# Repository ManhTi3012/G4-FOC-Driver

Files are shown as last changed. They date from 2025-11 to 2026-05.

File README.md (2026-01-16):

# ⚠️ **WARNING: PROJECT UNDER DEVELOPMENT, CHANGES WILL BE MADE**
<p align="center" style="display: flex; gap: 10px;">
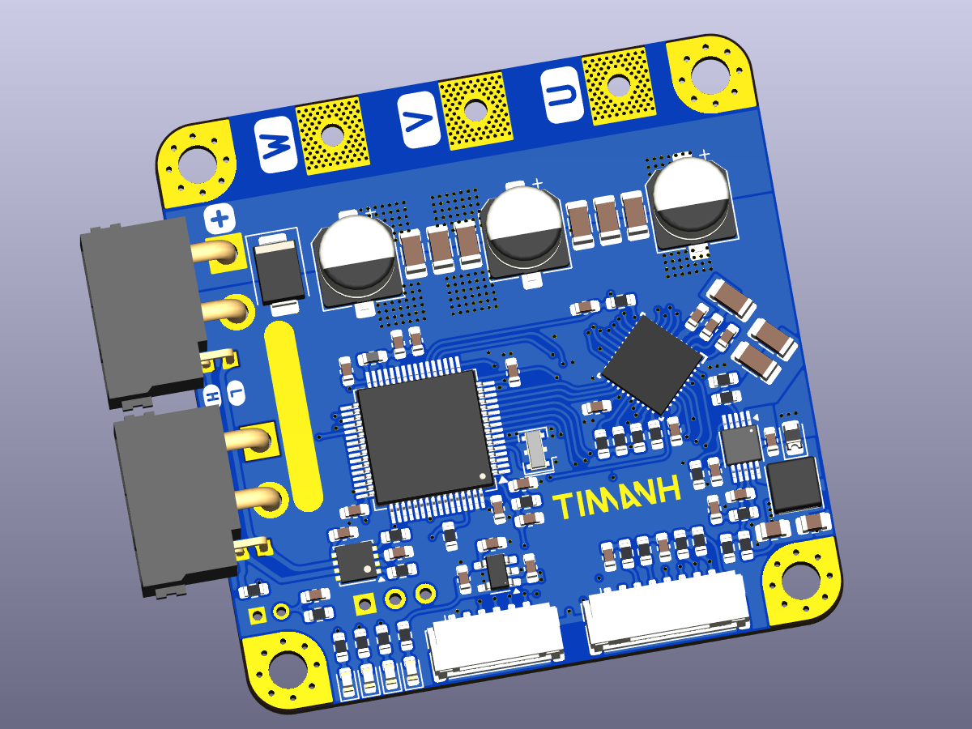
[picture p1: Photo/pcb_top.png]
  
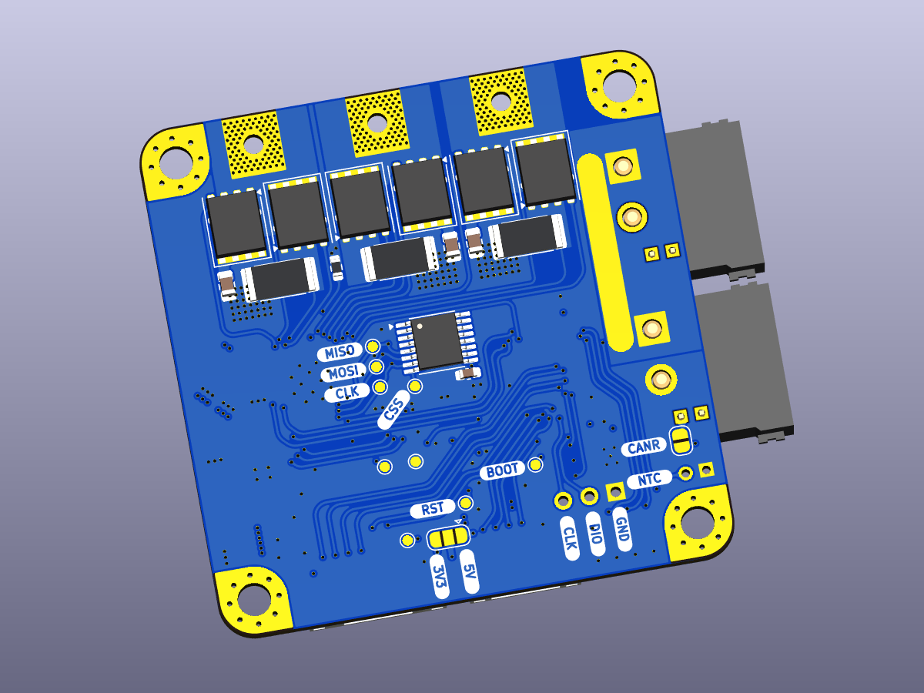
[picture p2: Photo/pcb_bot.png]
  
</p>

# G4-FOC-Driver

# Liability
* The software and hardware are still in development and may contain bugs, errors, or incomplete features.
* Users are encouraged to use this software and hardware responsibly and at their own risk.

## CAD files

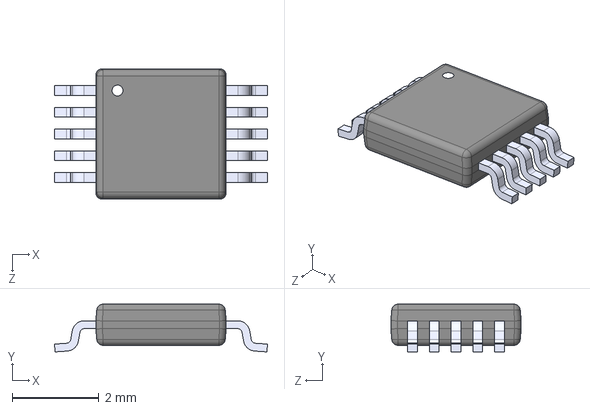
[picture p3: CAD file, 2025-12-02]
Dependencies/HVSSOP-10.STEP
4.90 x 1.10 x 3.00 mm

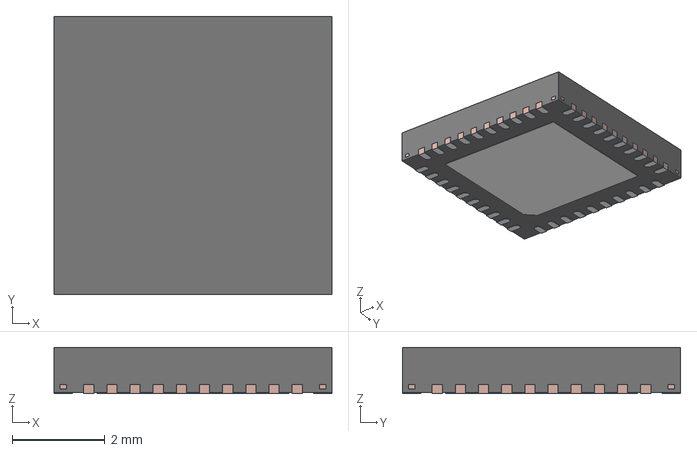
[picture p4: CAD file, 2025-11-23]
Dependencies/ul_DRV8323SRTAT/RTA0040B.stp
6.00 x 6.00 x 1.00 mm
FRAME

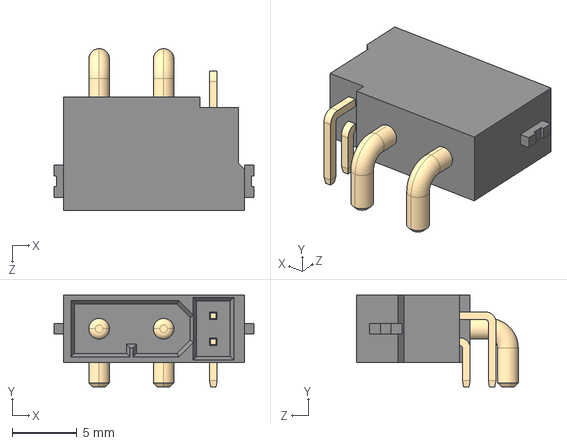
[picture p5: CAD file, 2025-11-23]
Dependencies/XT30PW_2_2_-M.G.B/XT30PW_2_2_-M.G.B.step
15.5 x 7.10 x 12.5 mm

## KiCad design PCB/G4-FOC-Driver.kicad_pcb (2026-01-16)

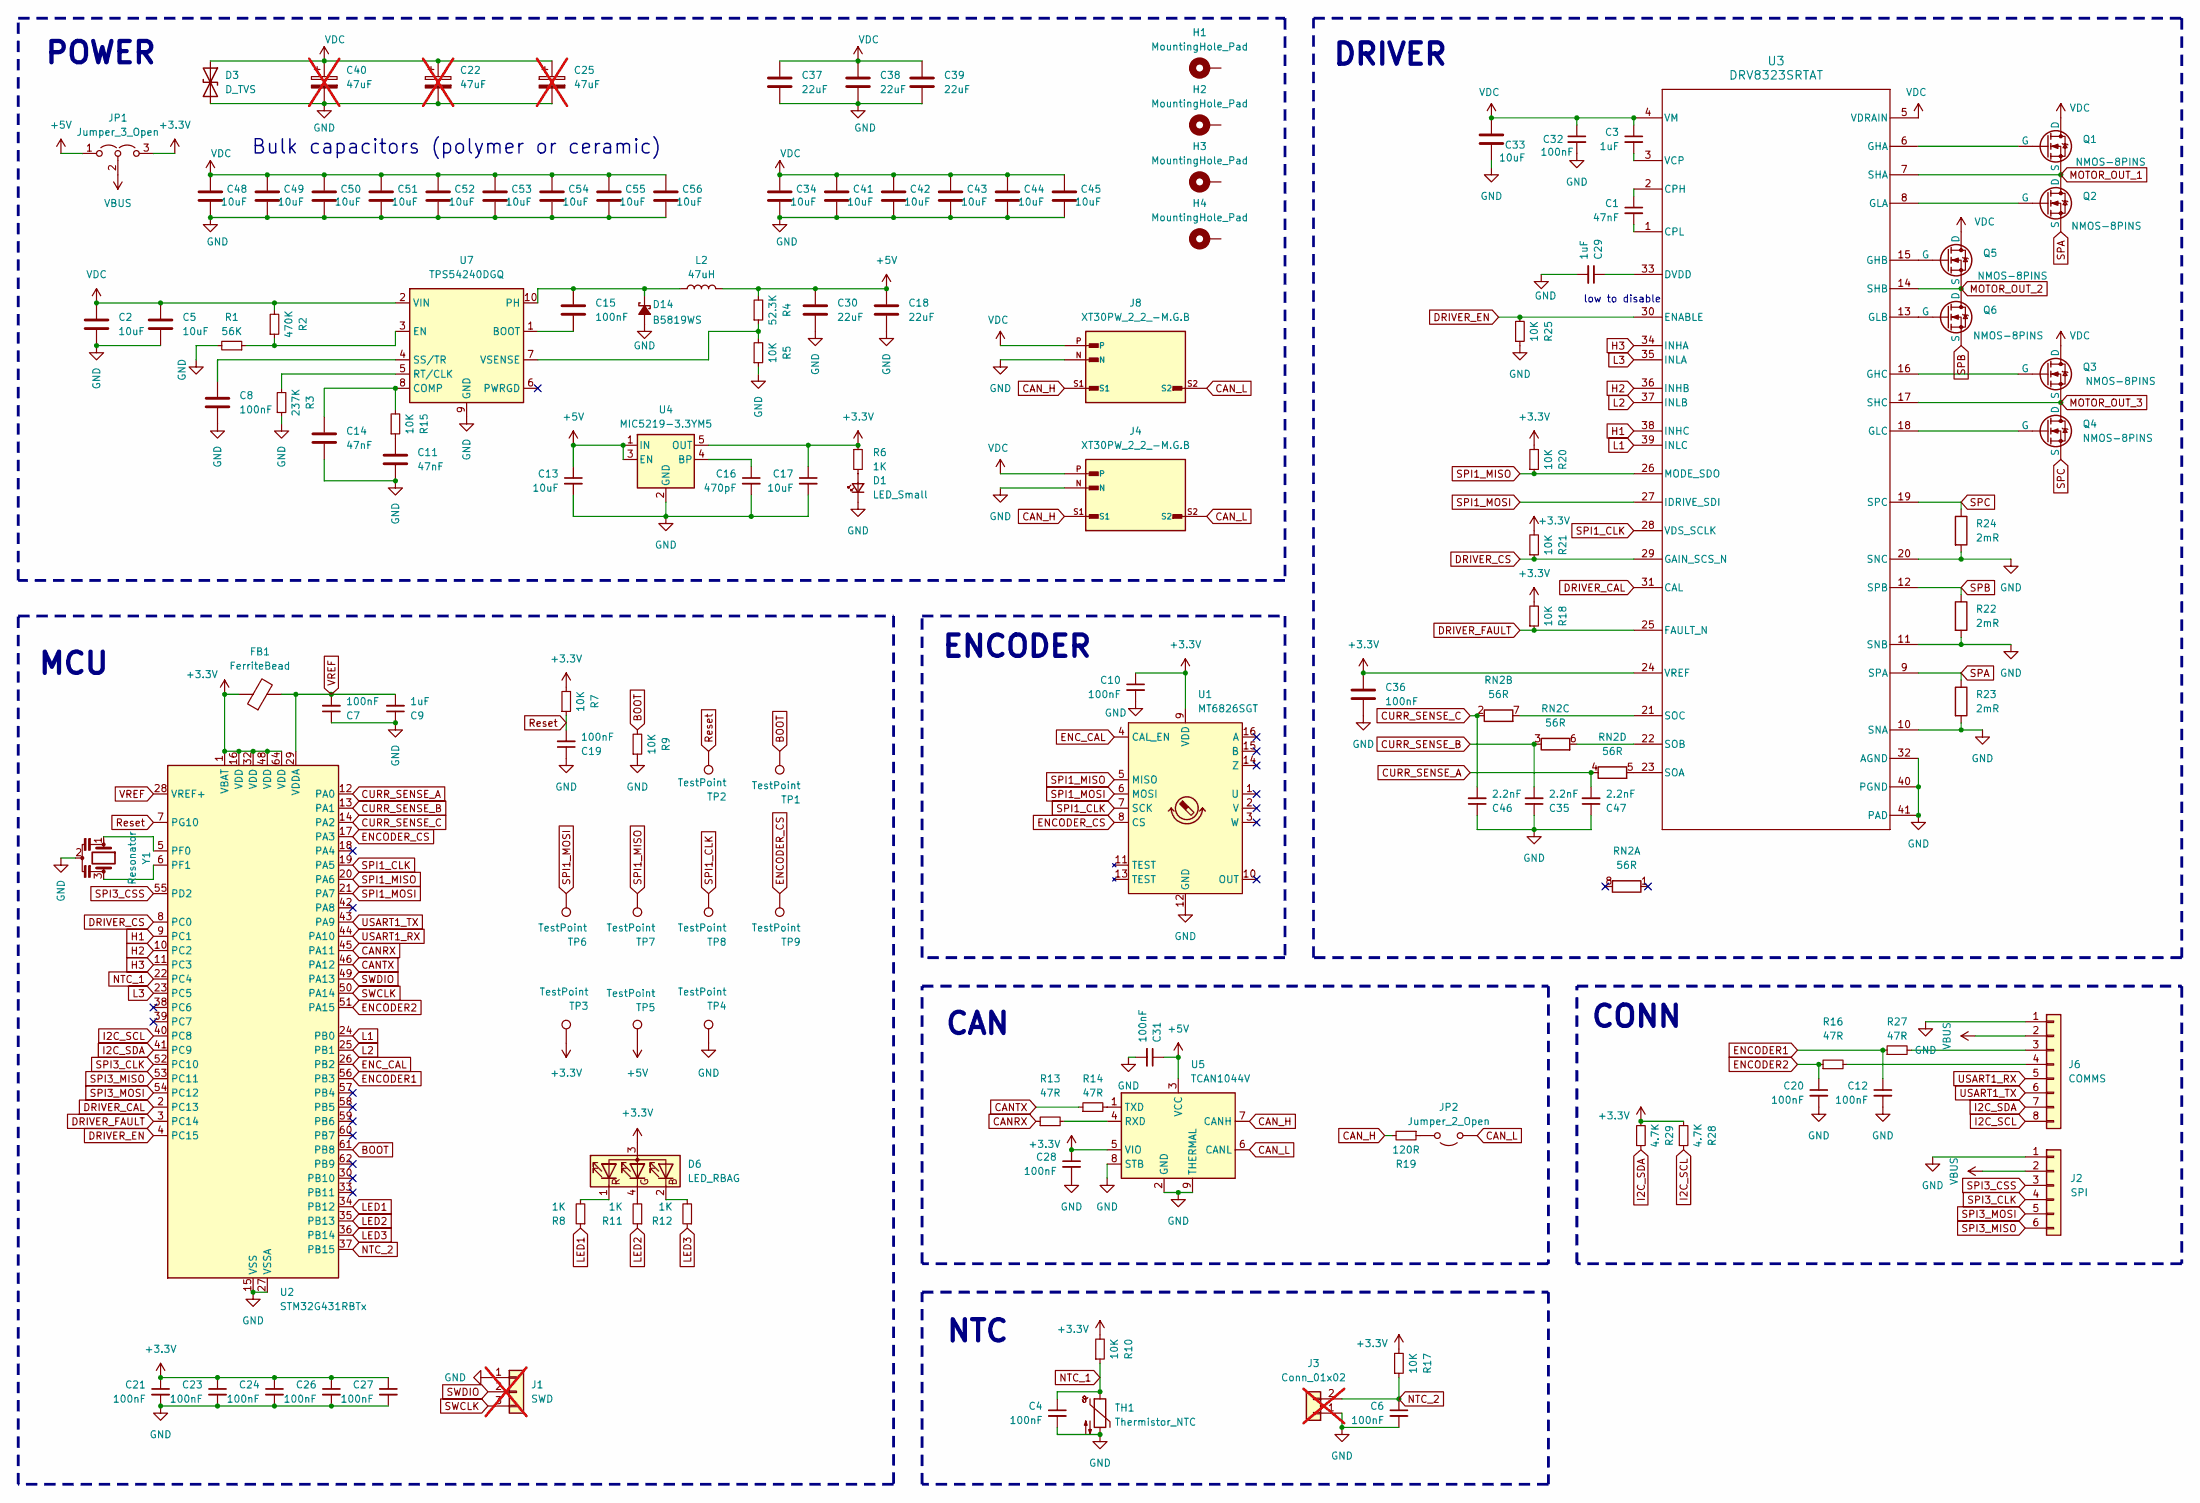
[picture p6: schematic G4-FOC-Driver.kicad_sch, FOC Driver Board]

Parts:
C1, C11, C14: 47nF; C_0603_1608Metric
C2, C5, C33, C34, C41, C42, C43, C44, C45, C48, C49, C50, C51, C52, C53, C54, C55, C56: 10uF; C_1206_3216Metric
C3, C9, C29: 1uF; C_0603_1608Metric
C4, C6, C7, C8, C10, C12, C15, C19, C20, C21, C23, C24, C26, C27, C28, C31, C32, C36: 100nF; C_0603_1608Metric
C13, C17: 10uF; C_0603_1608Metric
C16: 470pF; C_0603_1608Metric
C18, C30, C37, C38, C39: 22uF; C_0805_2012Metric
C22, C25, C40: 47uF; CP_Elec_6.3x5.9; not fitted
C35, C46, C47: 2.2nF; C_0603_1608Metric
D1: LED_Small; LED_0603_1608Metric
D3: D_TVS; D_SMB
D6: LED_RBAG; LED_Cree-PLCC4_2x2mm_CW
D14: B5819WS; D_0805_2012Metric
FB1: FerriteBead; L_0603_1608Metric
H1, H2, H3, H4: MountingHole_Pad; MountingHole_3.2mm_M3_Pad_Via
J1: SWD; PinHeader_1x03_P2.54mm_Vertical; not fitted
J2: SPI; JST_GH_SM06B-GHS-TB_1x06-1MP_P1.25mm_Horizontal
J3: Conn_01x02; PinHeader_1x02_P2.00mm_Vertical; not fitted
J4, J8: XT30PW_2_2_-M.G.B; AMASS_XT30PW_2_2_-M.G.B; PARTREV NA
J6: COMMS; JST_GH_SM08B-GHS-TB_1x08-1MP_P1.25mm_Horizontal
JP1: Jumper_3_Open; SolderJumper-3_P1.3mm_Open_RoundedPad1.0x1.5mm
JP2: Jumper_2_Open; SolderJumper-2_P1.3mm_Open_RoundedPad1.0x1.5mm
L2: 47uH; L_APV_ANR4020
Q1, Q2, Q3, Q4, Q5, Q6: NMOS-8PINS; PQFN-8-EP_6x5mm_P1.27mm_Generic
R1: 56K; R_0603_1608Metric
R2: 470K; R_0603_1608Metric
R3: 237K; R_0603_1608Metric
R4: 52.3K; R_0603_1608Metric
R5, R7, R9, R10, R15, R17, R18, R20, R21, R25: 10K; R_0603_1608Metric
R6, R8, R11, R12: 1K; R_0603_1608Metric
R13, R14, R16, R27: 47R; R_0603_1608Metric
R19: 120R; R_0603_1608Metric
R22, R23, R24: 2mR; R_2512_6332Metric
R28, R29: 4.7K; R_0603_1608Metric
RN2: 56R; R_Array_Convex_4x0402
TH1: Thermistor_NTC; R_0603_1608Metric
TP1, TP2, TP3, TP4, TP5, TP6, TP7, TP8, TP9: TestPoint; TestPoint_Pad_D1.0mm
U1: MT6826SGT; TSSOP-16_4.4x5mm_P0.65mm
U2: STM32G431RBTx; LQFP-64_10x10mm_P0.5mm
U3: DRV8323SRTAT; RTA0040B
U4: MIC5219-3.3YM5; SOT-23-5
U5: TCAN1044V; Texas_S-PVSON-N8_ThermalVias
U7: TPS54240DGQ; HVSSOP-10-1EP_3x3mm_P0.5mm_EP1.57x1.88mm_ThermalVias
Y1: Resonator; Resonator_SMD_Murata_CSTxExxV-3Pin_3.0x1.1mm

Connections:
+3.3V: C10.1, C17.1, C21.1, C23.1, C24.1, C26.1, C27.1, C28.1, C36.1, D6.3 (A), FB1.1, JP1.3 (B), R6.1, R7.2, R10.2, R17.2, R18.2, R20.2, R21.2, R28.2, R29.2, TP3.1, U1.9 (VDD), U2.1 (VBAT), U2.16 (VDD), U2.32 (VDD), U2.48 (VDD), U2.64 (VDD), U3.24 (VREF), U4.5 (OUT), U5.5 (VIO)
+5V: C13.1, C18.2, C30.2, C31.1, JP1.1 (A), L2.2, R4.2, TP5.1, U4.1 (IN), U4.3 (EN), U5.3 (VCC)
BOOT: R9.2, TP1.1, U2.61 (PB8)
CANRX: R13.1, U2.45 (PA11)
CANTX: R14.1, U2.46 (PA12)
CAN_H: J4.S1, J8.S1, R19.2, U5.7 (CANH)
CAN_L: J4.S2, J8.S2, JP2.1 (A), U5.6 (CANL)
CURR_SENSE_A: C47.2, RN2.4 (R4.1), U2.12 (PA0)
CURR_SENSE_B: C35.2, RN2.3 (R3.1), U2.13 (PA1)
CURR_SENSE_C: C46.2, RN2.2 (R2.1), U2.14 (PA2)
DRIVER_CAL: U2.2 (PC13), U3.31 (CAL)
DRIVER_CS: R21.1, U2.8 (PC0), U3.29 (GAIN_SCS_N)
DRIVER_EN: R25.2, U2.4 (PC15), U3.30 (ENABLE)
DRIVER_FAULT: R18.1, U2.3 (PC14), U3.25 (FAULT_N)
ENCODER1: C12.1, R27.1, U2.56 (PB3)
ENCODER2: C20.1, R16.1, U2.51 (PA15)
ENCODER_CS: TP9.1, U1.8 (CS), U2.17 (PA3)
ENC_CAL: U1.4 (CAL_EN), U2.26 (PB2)
GND: C2.1, C4.2, C5.1, C6.2, C7.1, C8.1, C9.1, C10.2, C11.1, C12.2, C13.2, C14.1, C16.2, C17.2, C18.1, C19.1, C20.2, C21.2, C22.2, C23.2, C24.2, C25.2, C26.2, C27.2, C28.2, C29.2, C30.1, C31.2, C32.2, C33.1, C34.1, C35.1, C36.2, C37.1, C38.1, C39.1, C40.2, C41.1, C42.1, C43.1, C44.1, C45.1, C46.1, C47.1, C48.1, C49.1, C50.1, C51.1, C52.1, C53.1, C54.1, C55.1, C56.1, D1.1 (K), D3.2 (A2), D14.2 (A), J1.1, J2.1, J3.1, J4.N, J6.1, J8.N, R1.2, R3.1, R5.1, R9.1, R22.2, R23.2, R24.2, R25.1, TH1.2, TP4.1, U1.12 (GND), U2.15 (VSS), U2.27 (VSSA), U2.31 (VSS), U2.47 (VSS), U2.63 (VSS), U3.10 (SNA), U3.11 (SNB), U3.20 (SNC), U3.32 (AGND), U3.40 (PGND), U3.41 (PAD), U4.2 (GND), U5.2 (GND), U5.8 (STB), U5.9 (THERMAL), U7.9 (GND), U7.11 (GND), Y1.2
H1: U2.9 (PC1), U3.38 (INHC)
H2: U2.10 (PC2), U3.36 (INHB)
H3: U2.11 (PC3), U3.34 (INHA)
I2C_SCL: J6.8, R28.1, U2.40 (PC8)
I2C_SDA: J6.7, R29.1, U2.41 (PC9)
L1: U2.24 (PB0), U3.39 (INLC)
L2: U2.25 (PB1), U3.37 (INLB)
L3: U2.23 (PC5), U3.35 (INLA)
LED1: R8.1, U2.34 (PB12)
LED2: R11.1, U2.35 (PB13)
LED3: R12.1, U2.36 (PB14)
MOTOR_OUT_1: Q1.1 (S), Q1.2 (S), Q1.3 (S), Q2.5 (D), U3.7 (SHA)
MOTOR_OUT_2: Q5.1 (S), Q5.2 (S), Q5.3 (S), Q6.5 (D), U3.14 (SHB)
MOTOR_OUT_3: Q3.1 (S), Q3.2 (S), Q3.3 (S), Q4.5 (D), U3.17 (SHC)
NTC_1: C4.1, R10.1, TH1.1, U2.22 (PC4)
NTC_2: C6.1, J3.2, R17.1, U2.37 (PB15)
unnamed: C11.2, R15.1
unnamed: D1.2 (A), R6.2
unnamed: D6.2 (BK), R12.2
unnamed: D6.4 (GK), R11.2
unnamed: D6.1 (RK), R8.2
unnamed: C15.2, D14.1 (K), L2.1, U7.10 (PH)
unnamed: J6.3, R27.2
unnamed: J6.4, R16.2
unnamed: JP2.2 (B), R19.1
unnamed: Q1.4 (G), U3.6 (GHA)
unnamed: Q2.4 (G), U3.8 (GLA)
unnamed: Q3.4 (G), U3.16 (GHC)
unnamed: Q4.4 (G), U3.18 (GLC)
unnamed: Q5.4 (G), U3.15 (GHB)
unnamed: Q6.4 (G), U3.13 (GLB)
unnamed: RN2.7 (R2.2), U3.21 (SOC)
unnamed: RN2.6 (R3.2), U3.22 (SOB)
unnamed: RN2.5 (R4.2), U3.23 (SOA)
unnamed: U2.5 (PF0), Y1.1
unnamed: U2.6 (PF1), Y1.3
unnamed: C1.1, U3.2 (CPH)
unnamed: C1.2, U3.1 (CPL)
unnamed: C29.1, U3.33 (DVDD)
unnamed: C3.2, U3.3 (VCP)
unnamed: C16.1, U4.4 (BP)
unnamed: R13.2, U5.4 (RXD)
unnamed: R14.2, U5.1 (TXD)
unnamed: C15.1, U7.1 (BOOT)
unnamed: C14.2, R15.2, U7.8 (COMP)
unnamed: R1.1, R2.1, U7.3 (EN)
unnamed: R3.2, U7.5 (RT/CLK)
unnamed: C8.2, U7.4 (SS/TR)
unnamed: R4.1, R5.2, U7.7 (VSENSE)
Reset: C19.2, R7.1, TP2.1, U2.7 (PG10)
SPA: Q2.1 (S), Q2.2 (S), Q2.3 (S), R23.1, U3.9 (SPA)
SPB: Q6.1 (S), Q6.2 (S), Q6.3 (S), R22.1, U3.12 (SPB)
SPC: Q4.1 (S), Q4.2 (S), Q4.3 (S), R24.1, U3.19 (SPC)
SPI1_CLK: TP8.1, U1.7 (SCK), U2.19 (PA5), U3.28 (VDS_SCLK)
SPI1_MISO: R20.1, TP7.1, U1.5 (MISO), U2.20 (PA6), U3.26 (MODE_SDO)
SPI1_MOSI: TP6.1, U1.6 (MOSI), U2.21 (PA7), U3.27 (IDRIVE_SDI)
SPI3_CLK: J2.4, U2.52 (PC10)
SPI3_CSS: J2.3, U2.55 (PD2)
SPI3_MISO: J2.6, U2.53 (PC11)
SPI3_MOSI: J2.5, U2.54 (PC12)
SWCLK: J1.3, U2.50 (PA14)
SWDIO: J1.2, U2.49 (PA13)
USART1_RX: J6.5, U2.44 (PA10)
USART1_TX: J6.6, U2.43 (PA9)
VBUS: J2.2, J6.2, JP1.2 (C)
VDC: C2.2, C3.1, C5.2, C22.1, C25.1, C32.1, C33.2, C34.2, C37.2, C38.2, C39.2, C40.1, C41.2, C42.2, C43.2, C44.2, C45.2, C48.2, C49.2, C50.2, C51.2, C52.2, C53.2, C54.2, C55.2, C56.2, D3.1 (A1), J4.P, J8.P, Q1.5 (D), Q3.5 (D), Q5.5 (D), R2.2, U3.4 (VM), U3.5 (VDRAIN), U7.2 (VIN)
VREF: C7.2, C9.2, FB1.2, U2.28 (VREF+), U2.29 (VDDA)

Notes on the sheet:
ENCODER
Bulk capacitors (polymer or ceramic)
MCU
NTC
POWER
low to disable
DRIVER
CAN
CONN

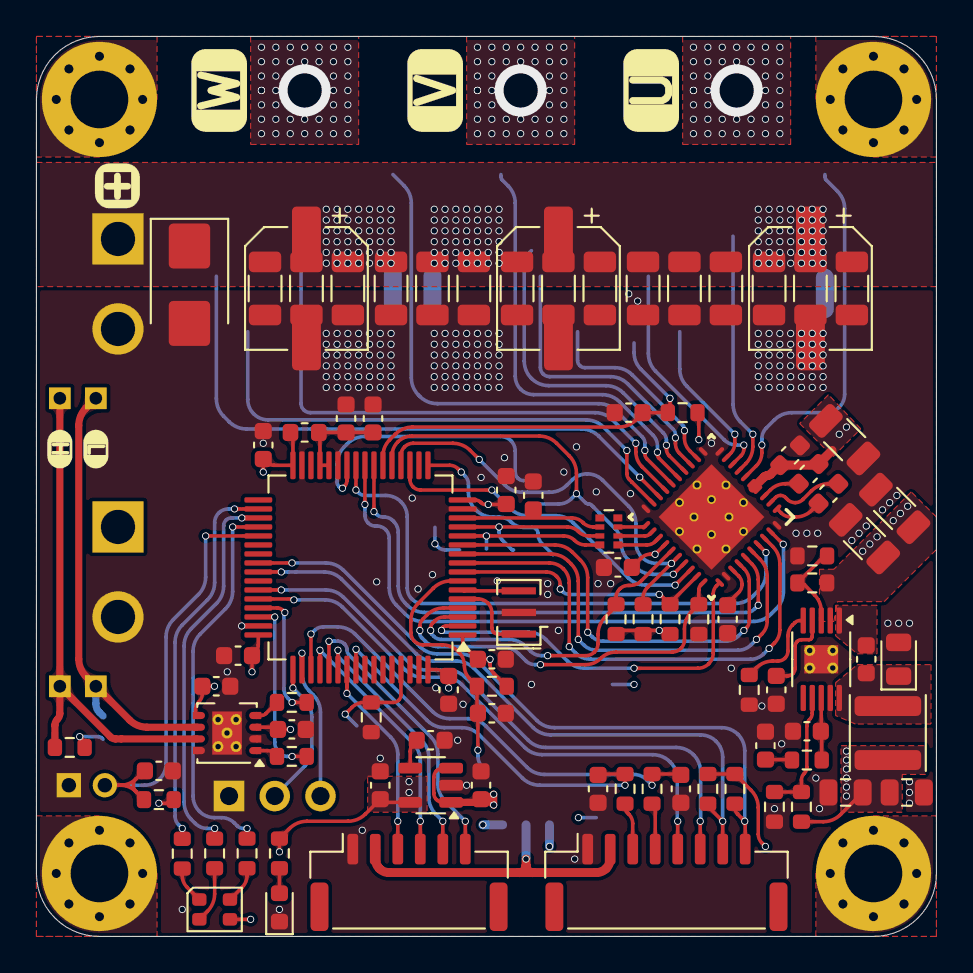
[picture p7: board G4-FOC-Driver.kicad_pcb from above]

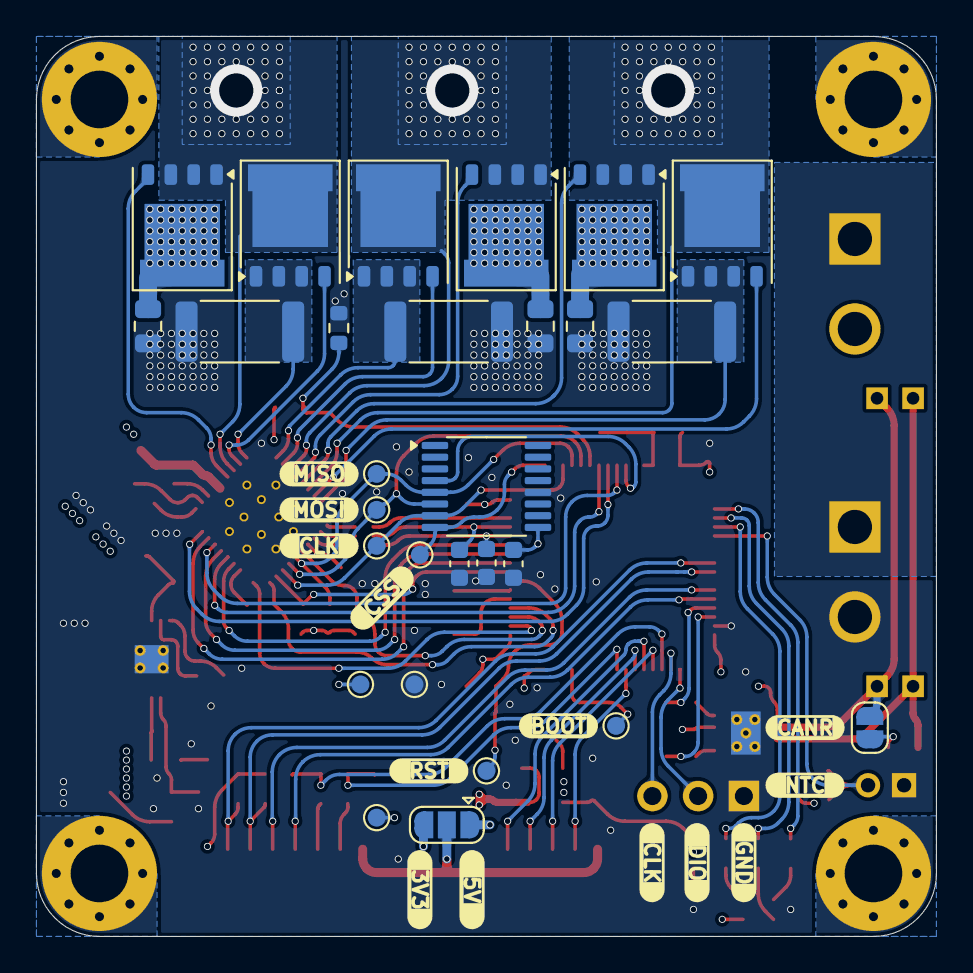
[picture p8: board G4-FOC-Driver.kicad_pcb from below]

Board: 4 copper layers, 50.0 x 50.0 mm, 126 parts (30 on the bottom side), 86 nets.

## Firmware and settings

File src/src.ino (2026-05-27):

#include <SimpleFOC.h>
#include "MagneticSensorMT6826.h"
#include "StatusLED.h"
// ===== Sensor =====
MagneticSensorMT6826 sensor(PA3);
StatusLED statusLED(PB14, PB12);

// ===== Serial =====
HardwareSerial Serial3(USART3);

// ===== Motor & Driver =====
BLDCMotor motor = BLDCMotor(20);
BLDCDriver6PWM driver = BLDCDriver6PWM(
  PC1, PB0,
  PC2, PB1,
  PC3, PC5,
  PC15
);

// ===== Commander =====
Commander command = Commander(Serial3);
void doTarget(char* cmd) { command.scalar(&motor.target, cmd); }

unsigned long long timer = 0;

void setup() {
  // ---- Serial ----
  Serial3.setTx(PA9);
  Serial3.setRx(PA10);
  Serial3.begin(115200);
  SimpleFOCDebug::enable(&Serial3);

  Serial3.println("MT6826 FOC torque test");

  // ---- Sensor ----
  sensor.init();
  motor.linkSensor(&sensor);
  Serial3.println("MT6826 ready");
  statusLED.begin();

  // ---- Driver ----
  driver.voltage_power_supply = 24.0f;
  driver.voltage_limit = 24.0f;
  driver.dead_zone = 0.05f;

  if (!driver.init()) {
    Serial3.println("Driver init failed!");
    while (1) {}
  }
  motor.linkDriver(&driver);
  Serial3.println("Driver ready!");

  // ---- Motor config ----
  motor.torque_controller = TorqueControlType::voltage;
  motor.controller = MotionControlType::angle;

  motor.voltage_limit = 24.0f;
  motor.voltage_sensor_align = 3.0f;

  // optional helpers
  motor.P_angle.P = 2.0;
  motor.P_angle.I = 0.1;
  motor.P_angle.D = 0.0;
  motor.PID_velocity.P = 0.3f;
  motor.PID_velocity.I = 2.0f;
  motor.PID_velocity.D = 0.0f;
  motor.LPF_velocity.Tf = 0.01f;
  motor.PID_velocity.output_ramp = 10.0f;

  // ---- Init ----
  motor.init();
  motor.initFOC();

  // ---- Commander ----
  command.add('T', doTarget, "target torque voltage");
  motor.useMonitoring(Serial3);

  motor.target = 3.14f;

  Serial3.println("Ready");
  Serial3.println("Try: T0.3  or  T1.0");
}

void loop() {
  if(millis() - timer > 2000){
    motor.target *= -1.0f;
    timer = millis();
  }
  motor.loopFOC();
  motor.move();
  command.run();
  statusLED.update();

  // sensor.update();
  // Serial3.println(sensor.getAngle());
}

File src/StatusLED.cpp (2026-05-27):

#include "StatusLED.h"

StatusLED::StatusLED(uint8_t bluePin, uint8_t redPin)
    : _bluePin(bluePin), _redPin(redPin) {}

void StatusLED::begin() {
    pinMode(_bluePin, OUTPUT);
    pinMode(_redPin, OUTPUT);

    digitalWrite(_bluePin, HIGH);
    digitalWrite(_redPin, HIGH);
}

void StatusLED::setFault(bool state) {
    _fault = state;
}

void StatusLED::update() {

    if (_fault) {
        digitalWrite(_bluePin, HIGH);
        digitalWrite(_redPin, LOW);
        return;
    }

    if (millis() - _timer > 500) {
        _timer = millis();

        _blinkState = !_blinkState;

        digitalWrite(_bluePin, _blinkState);
    }

    digitalWrite(_redPin, HIGH);
}

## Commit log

2025-11-09 Layout and component change
    [foc-motor-controller.kicad_pcb, foc-motor-controller.kicad_sch]
2025-12-03 clean up schematic
    [foc-motor-controller.kicad_pcb, foc-motor-controller.kicad_sch]
2025-12-04 Rename project from foc-motor-controller to G4-FOC-Driver
2025-12-06 clean up
    [Amass_XT30PW-M_pcb solder.stp, XT30(2+2)PW-M 3D DRAWING.STEP.STEP]
